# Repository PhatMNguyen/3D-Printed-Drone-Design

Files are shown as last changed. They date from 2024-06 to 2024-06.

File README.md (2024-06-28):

UTA has held the 3D-Printed Aircraft Competition (PAC) for eight years. A rotatory 
drone was 3D printed through additive manufacturing to compete in the 3D-printed aircraft 
competition. The drone was developed in several parts, including electronics, drone frame, arms, 
and drag device. Each component was designed and researched to be lightweight with minimal 
vibration and stiff structure. The electronics were chosen to ensure enough thrusting force and 
power to withstand the weight of the drone and drag device. The 3D filament chosen for the 
drone is abs, which was chosen based on its performance to heat, low density, and high elastic 
modulus, ensuring a stiff structure. Using topology optimization and solid works a 5” arm was 
created with stiffness and weight as our main objective. The drag device was created as a hinge, 
so the flaps were able to descend slowly, our main goal was to increase surface area without any 
electronic actuation. The design was further improved and tested through simulation and 
experimentation to ensure maximum stiffness, minimum frequencies, fast response and stable 
flight. The progression from the start to the final design took many iterations, but each iteration 
improved the overall design. The final iteration of our design was able to achieve 30 feet in the 8 
second time frame and a free fall time of 3 seconds.

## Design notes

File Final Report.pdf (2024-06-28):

# 3D Printed Drone Drone C Spring 2024

# Final Report

By
DESCENDER Inc.

Hoa Nguyen
Peter Nguyen
Yugesh Shrestha
Phat Nguyen
Cavin Van

Prepared for
Dr. Woods
Dr. Allsup
Dr. Taylor

May 3, 2024

Page | i

Abstract
UTA has held the 3D-Printed Aircraft Competition (PAC) for eight years. A rotatory drone was 3D printed through additive manufacturing to compete in the 3D-printed aircraft competition. The drone was developed in several parts, including electronics, drone frame, arms, and drag device. Each component was designed and researched to be lightweight with minimal vibration and stiff structure. The electronics were chosen to ensure enough thrusting force and power to withstand the weight of the drone and drag device. The 3D filament chosen for the drone is abs, which was chosen based on its performance to heat, low density, and high elastic modulus, ensuring a stiff structure. Using topology optimization and solid works a 5” arm was created with stiffness and weight as our main objective. The drag device was created as a hinge, so the flaps were able to descend slowly, our main goal was to increase surface area without any electronic actuation. The design was further improved and tested through simulation and experimentation to ensure maximum stiffness, minimum frequencies, fast response and stable flight. The progression from the start to the final design took many iterations, but each iteration improved the overall design. The final iteration of our design was able to achieve 30 feet in the 8 second time frame and a free fall time of 3 seconds.

Page | ii

Personnel

Hoa Nguyen
Lead Engineer
hoa.nguyen6@mavs.uta.edu

Peter Nguyen
Analysis Engineer
petertung.nguyen@mavs.uta.edu

Phat Nguyen
System Engineer
phat.nguyen4@mavs.uta.edu

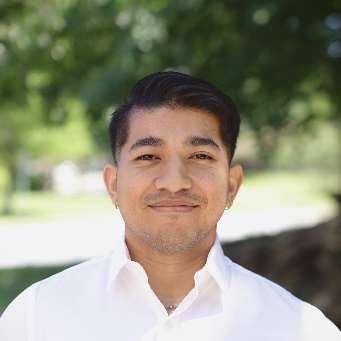
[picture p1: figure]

Yugesh Shrestha
Design Engineer
yugesh.shrestha@mavs.uta.edu

Cavin Van –
Manufacturing Engineer–
cavin.van@mavs.uta.edu

Faculty Advisors
Dr. Taylor
taylorrm@uta.edu

Dr. Allsup
thomas.allsup@uta.edu

Page | iii

Table of Contents

Page | iv

Nomenclature
a - Acceleration [m/s² ]
A - Surface Area [m²
| ]
C - Coefficient [-]
D - Drag Force [N]
F - Force [N]
g - Gravity [m/s² ]
H - Height [m]
L - Length of Arm [mm]
m - Mass [kg]
M - Moment [N*mm]
ρ - Density [kg/m³ ]
P - Power [W]
R - Reaction Force [N]
t - Time [s]
T - Torque [N*mm]
v - Velocity [m/s]
V - Shear [N]
ω | - Angular Velocity [rad/s]
x | - Location [mm]

Subscript
d | - Drag
f | - Final
i | - Initial
t | - Terminal
total - Total

Page | 1

### 1. Introduction

With the recent technological advancement of additive manufacturing, it has been widely popular in today’s manufacturing process. One form of additive manufacturing is called fused deposition modeling (FDM) 3D printing. With the advancement of FDM 3D Printing, it is widely used for rapid prototyping due to its consistency, reliability, and fast printing. Not only can FDM 3D printing be used for rapid prototyping, but it can also be another manufacturing method to produce parts for a product. With that, this project aims to use FDM 3D printing for rapid prototyping and producing a drone model that is completely 3D printed and functional.

### 2. Motivation

This is the 8th annual 3D-Printed Aircraft Competition (PAC) that UTA has hosted. Where students will compete to develop a 3D-printed aircraft using additive manufacturing. Currently, there are two aircraft categories: fixed and rotary wing. For the rotary wing category, students will create an aircraft where lift is generated by the propelling motion of the motors. Students will also compete in design and overall flight time when only 8 seconds of power is given to fly 30 feet. This means the team with the longest overall flight time, ascending and descending the aircraft, will win the competition.

Figure 1 Competition Poster

## 3DPAC 2024

8

th Annual
3D Printed Aircraft Competition
University of Texas at Arlington
Registration Open Now

Registration Deadline: January 31, 2024
Design Report Submission deadline: May 31, 2024 Aircraft check-in date: July 12, 1:00 to 4:00 p.m.
Flyoff Date: Saturday, July 13, 2024

Location: University of Texas at Arlington Maverick Stadium

Fixed Wing Category
All lifting surfaces must remain fixed • Altair Most Innovative Design*, $1000 • Longest duration flight, first prize, $1000 • Longest duration flight, second prize, $500 Each team must complete an entry form by the registration deadline. Rules and online entry: http://uta.engineering/3DPAC and https://www.asc-composites.org/competitions For informative videos on how to accomplish lightweighting, optimization, and analysis in Altair Inspire, go to https://www.youtube.com/watch?v=knB5rH1usr4. For Questions or Sponsorship Inquiries: Robert Taylor (taylorrm@uta.edu) *Design reports must be received by submission deadline to be eligible for Altair Most Innovative Design Awards

Rotary Wing Category
A significant proportion of lift is generated by rotation of components or of the entire body • Altair Most Innovative Design*, $1000 • Longest duration flight, first prize, $1000 • Longest duration flight, second prize, $500

Page | 2

The goal is to create the final drone product to compete in the rotary aircraft category and fly off on July 13, 2024. The project aims to win the longest flight duration using the 3D-printed drag device and drone.

### 3. Theory

### 3.1. Drone Arm

The drone arm can be seen as a cantilever beam supported by the frame. When a propeller is added to a motor, the lift load is applied to the arms' ends. Figure [x] displays the arm's free-body diagram.

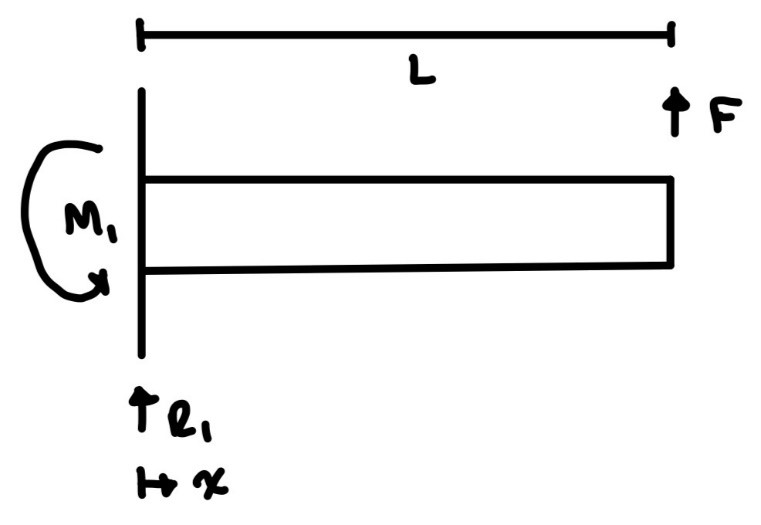
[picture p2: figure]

Figure 2 Free-Body Diagram of Drone Arm

To calculate the reaction forces, use the principle of equilibrium and have the sum of forces equal zero. The resultant forces can be found below.

R = F

M = F ∗ L

With the help of singularity equations, shear and moment can be found in the equation below.

V = M < x >+ R − F < x − L >

M = −M + Rx − F < x − L >

Page | 3

With the full analysis of this equation, the max shear will occur throughout the whole arm. The max moment will occur at the resultant forces; this is useful to determine the length of the arm to minimize this moment.

### 3.2. Drag Device

The design of the drag device was based on increasing the surface area to increase the drag force experienced by the device, which would lead to an increase in descent time. Descent time was calculated first by determining the terminal velocity that the device was traveling before hitting the ground. The formula used to calculate the terminal velocity of the device is shown below.
v =
2W
CρA

Where Vt is the terminal velocity of the device once it enters free fall, ρ is the density of the air, A is the surface area of the drag device, and W is the weight, C is the drag coefficient of the drag device.

Initially, the flat plate's drag coefficient was used to calculate the terminal velocity. Weight was calculated by determining the material's volume and density. The gravity and density of the air at 90 degrees Fahrenheit at a Latitude of 32.73, a longitude of -97.11, and an elevation of 189.89 above sea level were used.

Time of descent was calculated in two phases; 1st phase was when it took the device to get to terminal velocity from the free fall, and 2nd phase was when it took the device to hit the ground after reaching terminal velocity. The formula used for this calculation is as follows:

1

st phase:

t =

v − v
g

where the initial velocity is zero, the final velocity is the terminal velocity, and g is the acceleration due to gravity. The distance traveled to reach terminal velocity was also calculated using the following formula shown below:

H =

v

− v

2g

2

nd phase:
Given that the drone is estimated to drop from a height of 9.14m (30ft), the time it took to reach the ground after reaching terminal velocity was calculated using the following formula.

Page | 4

t =

9.14 − H
v

The total time of descent was calculated by adding those two times together.

t = t + t

### 4. Design

### 4.1. Drone Specification

Protecting the electronic components in the drone body was ideal. A modular design, where the arms can be replaced, would have been ideal if the arms had been destroyed in the flight tests. A lower center of gravity is crucial to the design as it helps the overall stability of the device. A stiff structure reduces vibrations in the system, or instability can occur.

### 4.2. Drag Device Specification

The drag device was designed by keeping the weight of the device and the drone’s main body in mind. The goal was to stay under 600 g for the entire assembly. Weight reduction was also achieved by having the drag device deploy with the help of air resistance instead of servos.

### 4.3. Electronic Specification

- Flysky remote control and receiver.
This allows the remote controller to communicate with the drone and receive any controls.
- 4 Cells LiPo battery; 650mAh, 90C, 15.8V
A 650mAh (0.65Ah) battery with a 90C discharge rate can provide 90 times its capacity. So, 90 x 0.65Ah = 58.5A, which means the battery can safely provide 58.5A amps of current for 30 seconds.
- Xing 2208 1800kv motors
2208 => stator’s diameter = 22mm and height = 8mm, 1800kv=> 1800 rpm per volt of the power supply. KV rating indicates the motor’s RPM per volt. At 22.2V, the motor’s theoretical maximum RPM is 1800 * 14.8 = 26640 RPM.
- Nazgul F5 – Tri Blade Propeller – 5.0x3.5x3
5-inch diameter = 0.127, 3.5-inch pitch
- SpeedyBee F405 V4 BLS 55A 30x30 FC&ESC Stack

Verification:

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

Page | 6

=> total discℎarge rate = 12

=> Battery time ∶ 225s

So, with the chosen components, the motor can produce sufficient power to achieve the goal with a discharge rate of 12. The thrust calculation was computed with a blade efficiency of 80%. Blade-Element Theory (BET) and Vortex theory must be considered for more accurate thrust predictions. The theoretical battery time is calculated to be 225 seconds, equivalent to 3.75 minutes, sufficient for three flights in competition.

Torque (τ) calculation:

Power (P) =

τ
ω

=> τ = Pω = 16W ∗ 4185.5

rad
s

= 66968 N ∗ m = 66.96N ∗ mm

### 4.4. Material Selection

The materials investigated for this project were TPU, PLA, PETG, and ABS. The main criteria for choosing a material were based on a high heat resistance material, high elastic modulus, and low density.

Table 1 Material Properties

Materials | Heat Resistance Temperature (C) | Elastic Modulus (MPa) | Density (g/cm³ )
TPU | N/A | N/A | 1.22
ABS | 87 | 1880 | 1.05
PLA | 57 | 2750 | 1.24
PTEG | 69 | 1670 | 1.25

A highly heat-resistant material would be more resistant to softening as temperature increases. Materials with low heat resistance would likely soften and deform in the summer. For instance, PLA is affected by UV light weathering, which reduces the material's softening temperature, so using PLA for the final device is not advised. However, because PLA is very easy to use when 3D printing, it is ideal for prototyping compared to the other materials.

Investigating the material's elastic modulus can achieve high stiffness, resulting in the arms having a very small deflection when loads are applied. The best materials would be ABS and PLA because they would allow for higher stiffness in the arms, whereas TPU is very elastic and works best as a damper.

Page | 7

A material with the lowest density would allow the drone to be lightweight, increasing the time of our descent. ABS was chosen because it has the highest heat resistance temperature, the lowest density, and the second-highest elastic modulus.

### 4.5. Arm Design 1

The first design is displayed in Figure 3. This model ultimately did not work, as the arms were too long and caused the structure to break at the root of the arms. With that, it was too heavy and was weak when it came to torsional. A vibration test was run to determine if the system would experience any vibrations. The results from the vibration test showed that there were vibrations in the system, which would cause instability. So, a redesign of the arms will be considered to combat the vibration issues.

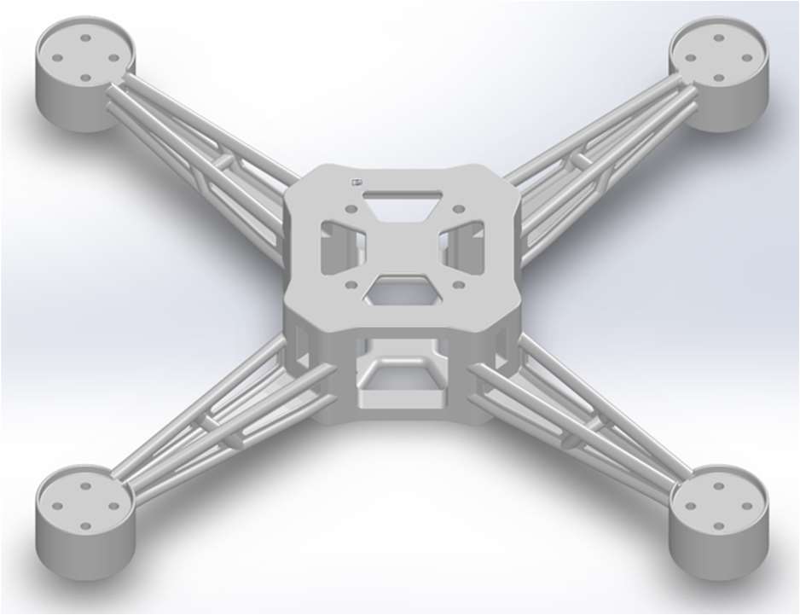
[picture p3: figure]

Figure 3 1st Iteration Arm

### 4.6. Arm Design 2

From the first design, where there were issues at the root, the drone arm length was shortened to reduce the moment at the root. The design goal of the arms is to keep them stiff and lightweight. With the help of topology optimization, the drone arm was designed and shown in Figure 4. The second iteration is designed to be stiff to combat the forces of lift and torsional at the end. Overall, this is a better design than the previous iteration due to its reduced moment at the root, stiffness, and lightweight. This structure will also help reduce vibrations experienced in the first iteration.

Page | 8

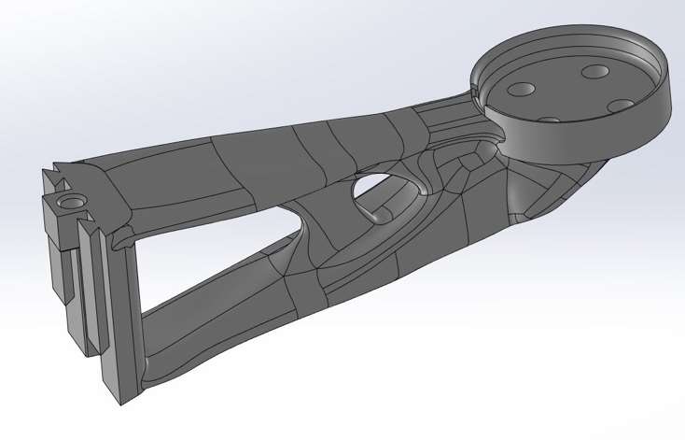
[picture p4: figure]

Figure 4 2nd Iteration Arm

### 4.7. Drag Device Design 1

The initial prototype of the drag device was created based on a modular design. The circular flaps at the end of the arms were to generate drag force. The arms could rotate vertically about the point of contact at the base. This design choice was made so that the drag device would deploy with the help of air resistance. During numerous tests of this prototype, it was observed that the circular flaps did not generate enough drag for the drag device to slow down. Still, the arm's ability to rotate vertically during deployment made the descent stable possible.

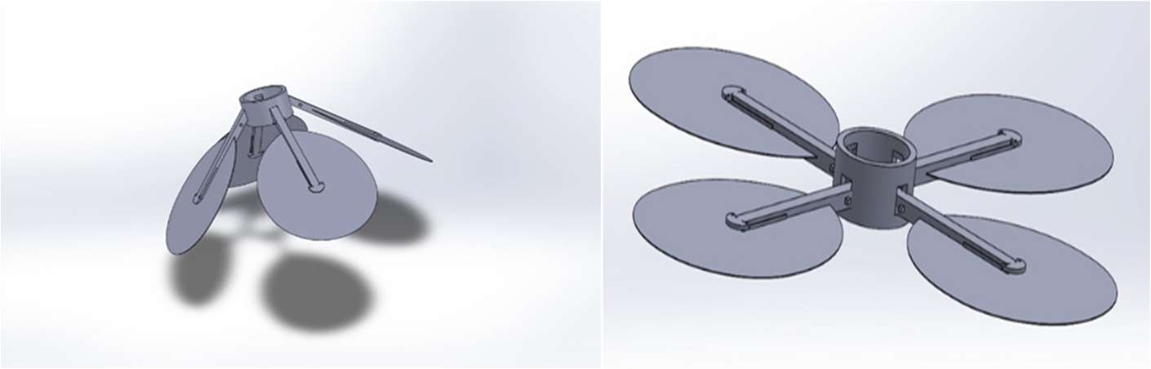
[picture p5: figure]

Figure 5 1st Concept of Drag Device

### 4.8. Drag Device Design 2

The second prototype was designed to direct the airflow underneath the drag device. The motivation for designing this prototype was taken from the sugar glider’s gliding motion during free fall. The curved wing design was incorporated to direct the airflow outwards from the center cross-section to achieve drag. While testing this prototype, the amount of surface area of the device helped generate enough drag force to slow down the device, but it was observed that the device had unstable descent on multiple test runs. The inability of the air to pass through the center created turbulence, which was the main reason for the unstable descent. Fixed wings also meant the rotors could not direct air to the ground to generate enough lift for the drone to fly.

Page | 9

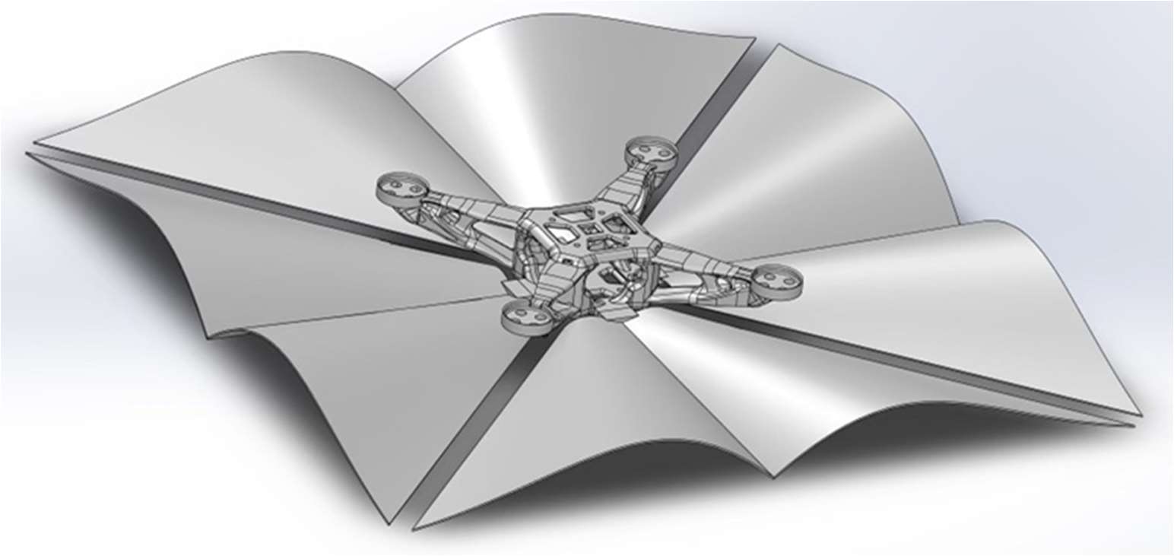
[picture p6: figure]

Figure 6 2nd Concept of Drag Device

### 4.9. Drag Device Final Design

The final design of the drag device was a collaboration of two previously designed prototype ideas. The flaps from the 2nd prototype were incorporated to deploy only due to air resistance. The hinge-like design between the flaps and the drag arm helped the flaps to rotate about the point of contact. Constraints for how much rotation the flaps can make were created by introducing stoppers on the arms, which also dictated the flaps' deflection. Positioning radially outward flaps helped create space at the center of the device, which would be crucial in directing airflow through the center. Pillar structures were assimilated between the drone and drag arms to support and stabilize the structure.

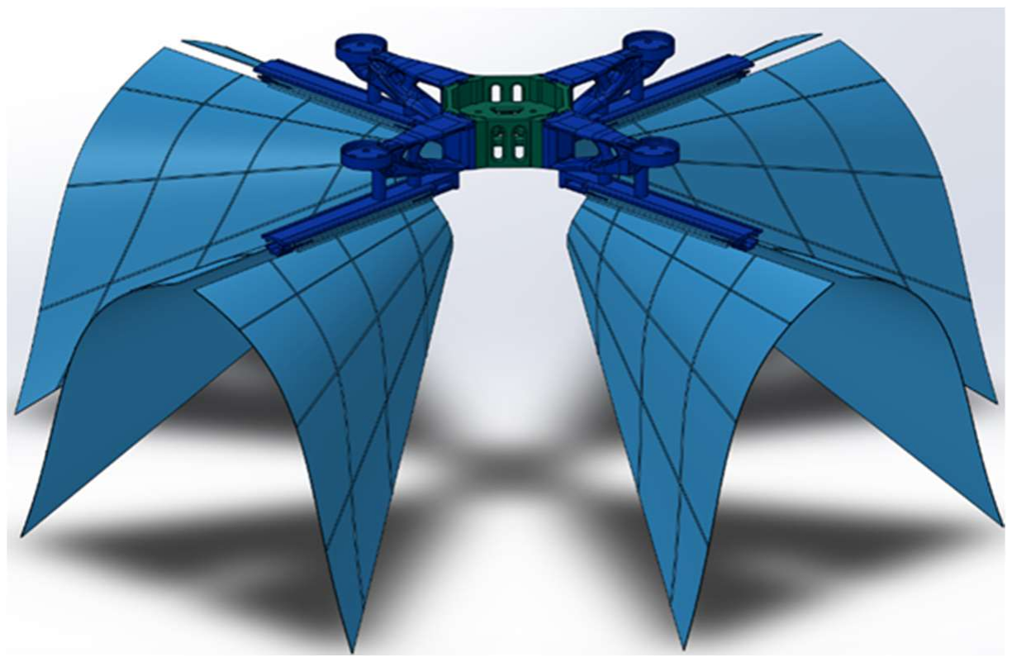
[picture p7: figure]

Figure 7 Current Design

Page | 10

### 5. Analysis

### 5.1. Drone Arm 2

The quadcopter drone's structural integrity and performance were evaluated using finite element analysis on ANSYS. For structural analysis, the purpose was to examine the drone's behavior under different loading conditions, including its weight and aerodynamic forces, such as the thrust force. The drone's weight acts as a downward force at the center mass of the drone. The thrust force from each propeller generates lift and acts as an upward force. Each arm was modeled as a cantilever beam, fixed at one end and free at the other. There were fixed supports placed at the screw holes of each arm, where it was connected to the base of the drone. The lifting force and weight were also accounted for.
The structural analysis results calculated the total deformation, Von Mises stresses, and safety factor. The results of total deformation showed a uniform deformation, where a maximum total deformation of 0.063 mm occurred at the propellers and decreased uniformly towards the screw holes to a minimum total deformation of 0 mm. It signifies that the drone had a high stiffness. A safety factor of 15 indicates that the drone was overdesigned, with unexpected loads. Although these were the results for the safety factor in ANSYS, the safety factor for the actual drone decreased due to the infill percentage, assuming solid infill when 3D printing the drone.

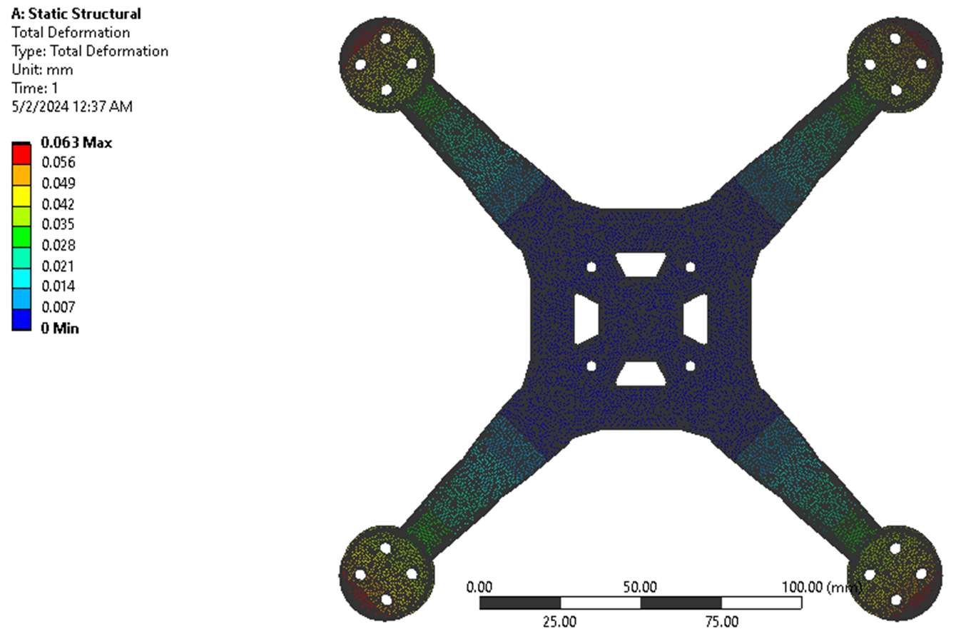
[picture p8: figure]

Figure 8 Total Deformation for Static Structural

Using Modal analysis in ANSYS, the drone's dynamic structure was identified by the mode shapes and their natural frequencies at different dynamic loadings or sinusoidal inputs of varying frequencies. This is where the structure experienced high-level vibrations and critical areas to add stiffeners to the part.

Page | 11

The analysis's results showed that the critical areas were at the ends of the arms, where it acted like a fixed free cantilever beam with loading applied at the free end. It showed that it is more likely to deflect at the tip at different dynamic loadings. The results showed that at the lowest frequency of 451 Hz, it would most likely resonate and vibrate, ultimately leading to stability and part failure when flying the aircraft. For the drone with the propellers and motors, it never reached 451 Hz, so the drone did not cause vibrations.

Figure 9 Total Deformation for Modal

### 5.2. Drag Device

Computational fluid dynamics simulation was conducted in SolidWorks using flow simulation. During the simulation, a metric unit system was chosen, and an external analysis was conducted with gravity turned on in the negative Y direction. The fluid for the simulation was air, and the terminal velocity of the device and its direction were entered. The type of flow was assumed to be laminar for this experiment. An Automatic Computational domain was created to conduct the Drag experiment. The global goal was created to track normal force in the Y direction, and the equation was entered to obtain the drag coefficient. The equation used to calculate the drag coefficient is shown below:

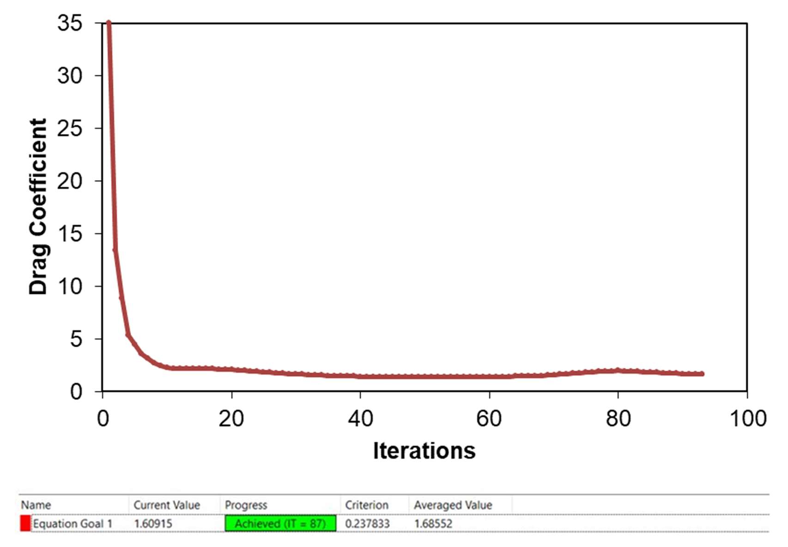
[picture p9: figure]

Page | 12

C =

2D
V

ρA

Where, C is the drag coefficient, D is the drag force, Vt is terminal velocity, ρ is the density of the air, and A is the device's surface area.
Quality Mesh is created to obtain adequate results for the calculations. Refinements were placed in a region surrounding the flaps because they are essential to the device's function.
Once the simulation started, plots were created, and the program continued running the simulation until the goal values, i.e., the Drag coefficient in this case, converged. A graph of converging values is shown in the figure below:

Figure 10 CFD Analysis Results

From 87 iterations, the average value of the drag coefficient was 1.69.

Cutting plots on the results helped to select the plane and parameter we wanted to inspect, which were shown in color contours depending on the values. Velocity distribution around the drag device is shown in the figure below:

Page | 13

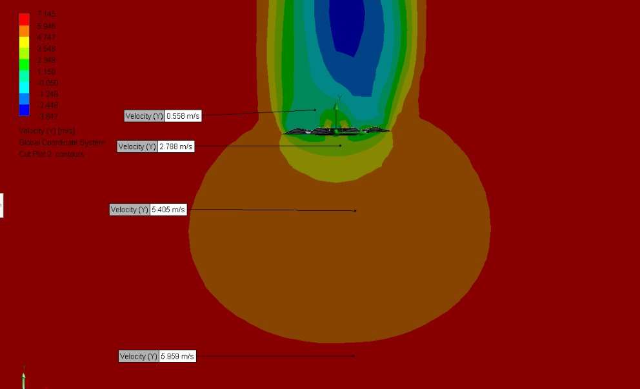
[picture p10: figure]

Figure 11 CFD Analysis

The drag coefficient obtained from the flow simulation was used to calculate the drag device's descent time. The table below shows the descent time of the drag device with an
increase in surface area.

Table 2 Time of Descend Calculation Based on Surface Area

Length (m) | Area (m² ) | Vt (m/s) | Drag force (N) | Time to reach Vt (s) | Distance to reach Vt (m) | Time to landing (s) | Distance to landing (m) | Total time for descent (s)
0.3 | 0.09 | 6.58 | 3.79 | 0.67 | 2.21 | 1.05 | 6.93 | 1.73
0.4 | 0.16 | 5.21 | 4.22 | 0.53 | 1.39 | 1.49 | 7.76 | 2.02
0.5 | 0.25 | 4.44 | 4.77 | 0.45 | 1.00 | 1.84 | 8.14 | 2.29
0.6 | 0.36 | 3.95 | 5.45 | 0.40 | 0.80 | 2.11 | 8.35 | 2.52
0.7 | 0.49 | 3.63 | 6.26 | 0.37 | 0.67 | 2.34 | 8.47 | 2.71
0.8 | 0.64 | 3.40 | 7.18 | 0.35 | 0.59 | 2.52 | 8.55 | 2.86
0.9 | 0.81 | 3.23 | 8.23 | 0.33 | 0.53 | 2.66 | 8.61 | 2.99
1 | 1 | 3.11 | 9.40 | 0.32 | 0.49 | 2.78 | 8.65 | 3.10

Page | 14

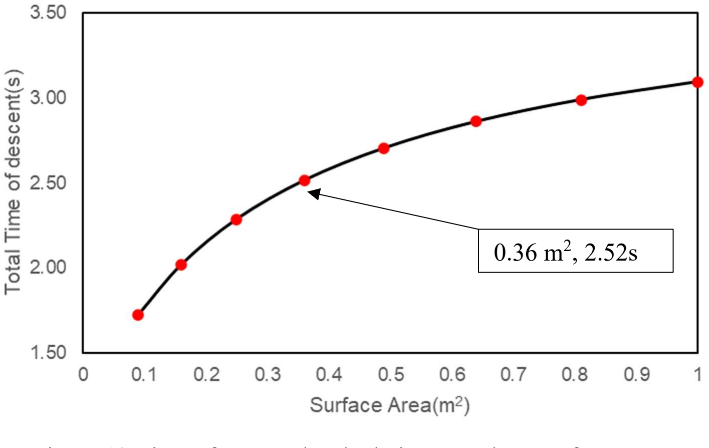
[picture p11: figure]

Figure 12 Time of Descend Calculation Based on Surface Area

### 6. Testing

### 6.1. Vibration Testing

During this test, the propellers will be removed from the drone, and the motors will be powered from 100 % and decreased to 40%. The structure will then be placed on a firm flat surface. During this test, it is important to observe any vibrations that the structure may encounter when the motors are at a constant 40% power. For the 1st iteration of the arms, it was found that there were vibrations present in the test. This led to the redesign of the arms, which led to the 2nd iteration. With the repetition of this test, the 2nd iteration arm did not encounter any vibrations.

### 6.2. Flight Testing

The drone could fly upward and downward without many stability issues during its launch. This means sufficient power is supplied to the motors, and the drone's weight is adequate for takeoff. It also has a faster response time and minimizes overshooting and system instability. There were also no implications with the drag device and drone when ascending upward because the drag device did not open until free fall.

Page | 15

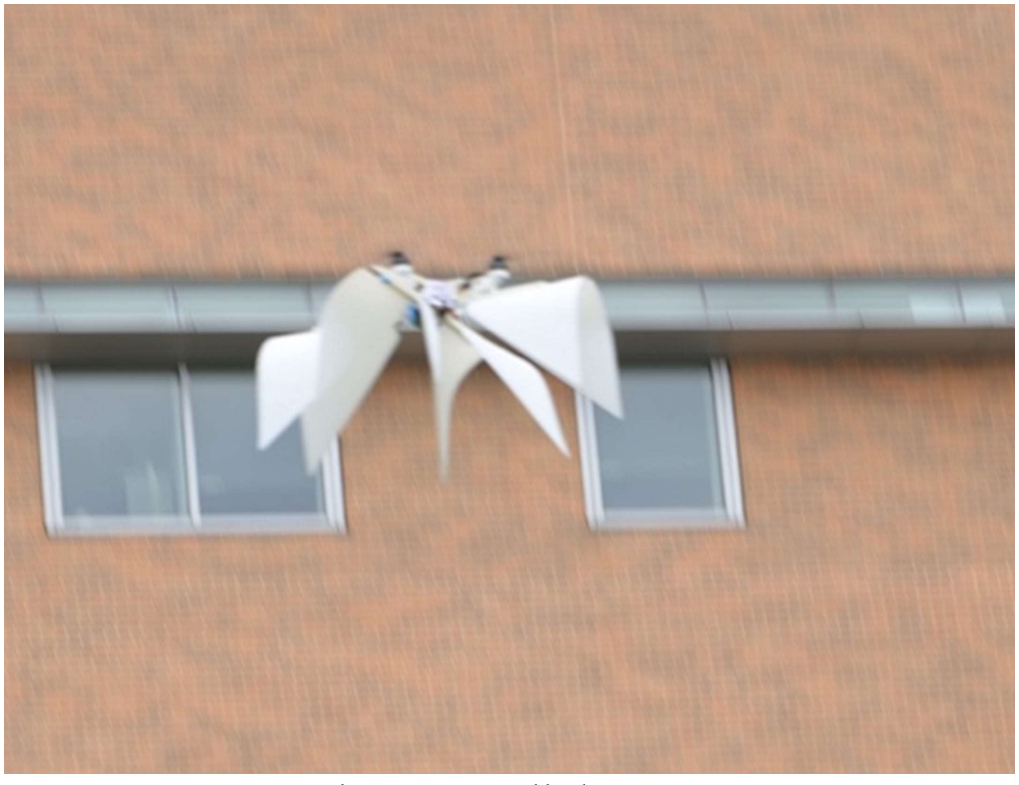
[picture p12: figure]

Figure 13 Flight Test

### 6.3. Drop Test

During the drone's descent and its drag device counterpart, the free fall time was 3 seconds. This fall time exceeded the calculated time of 2.52 seconds based on the 600 mm flaps. During the drag device's descent, the flaps worked just as anticipated, actuating like a hinge mechanism. During the drone’s descent, the flaps are met with air resistance, which opens the flaps, creating a drag force that slows the drone’s fall.

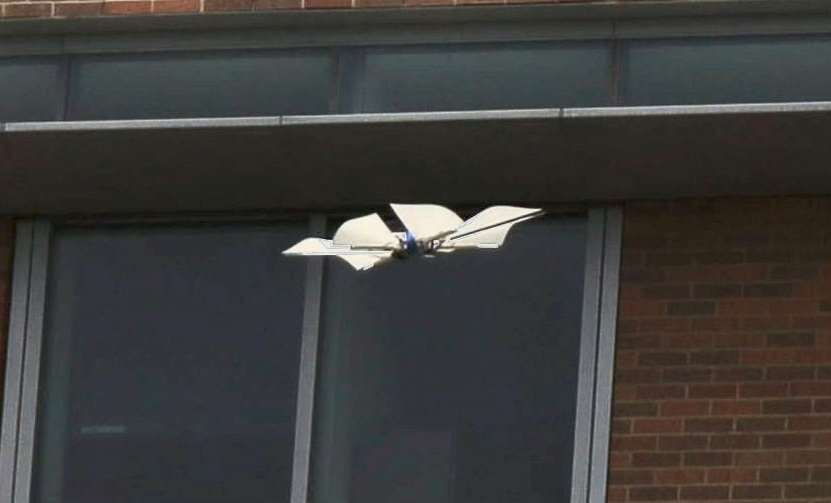
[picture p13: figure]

Figure 14 Drop Test

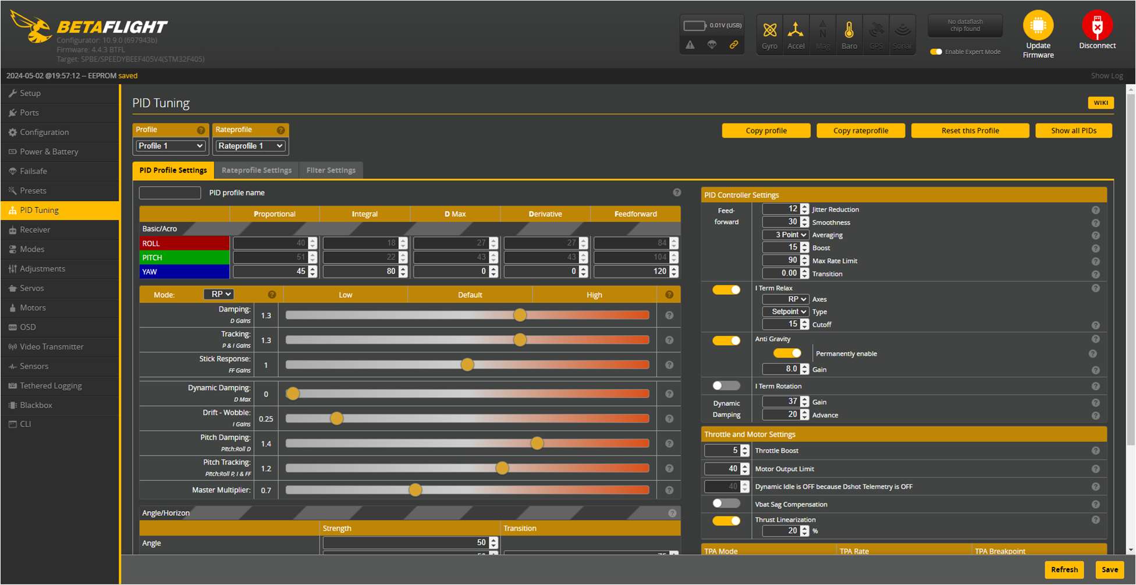
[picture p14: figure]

Page | 16

### 6.4. PID Tunning

Betaflight is utilized for Drone PID tuning, with adjustments made using the following sliders:

Figure 15 Betaflight Software

The tuning process begins by setting the initial tracking P&I slider value at 0.5, which is then incremented by 0.1 for each iteration. Flight tests are conducted for every increment to collect data into the drone’s Blackbox for dynamic response analysis in MATLAB. The responses are recorded for P &I slider values ranging from 0.5 to 1.3.

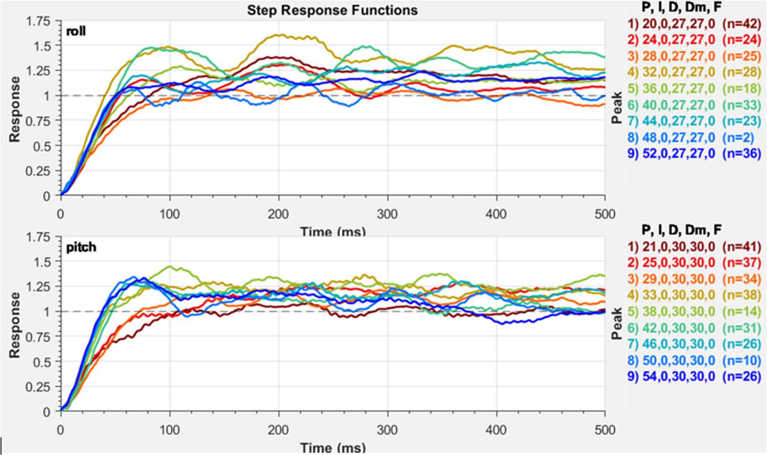
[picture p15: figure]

Page | 17

Figure 16 Dynamic Responses Corresponding to Slider Values

Among the responses, a value of 1.3 is chosen for its fast response and minimal oscillation for further tunning. However, a small steady-state error is observed in the roll response, and there is an overshot in the pitch response. To address these issues, the I-gain is increased for roll, and D-gain for pitch. The I-gain for Roll is adjusted by manipulating the "Drift-Wobble" slider, and the D-gain for Pitch is adjusted by manipulating the "Pitch damping" slider, using the same approach as adjusting the P&I slider.

Table 3 Sliders Values for Pitch Damping Test

Test Flight | Damping D Gain | Tracking P & I Gain | Stick Response | Dynamic Damping | Drift – Wobble | Pitch Damping | Pitch Tracking | Master Tracking
1 | 0.6 | 1 | 0 | 0 | 0 | 1 | 1 | 1
2 | 0.8 | 1 | 0 | 0 | 0 | 1 | 1 | 1
3 | 1.0 | 1 | 0 | 0 | 0 | 1 | 1 | 1
4 | 1.2 | 1 | 0 | 0 | 0 | 1 | 1 | 1
5 | 1.4 | 1 | 0 | 0 | 0 | 1 | 1 | 1
6 | 1.1 | 1 | 0 | 0 | 0 | 1 | 1 | 1

Page | 18

Table 4 Sliders Values for Multiplier Test

Test Flight | Damping D Gain | Tracking P & I Gain | Stick Response | Dynamic Damping | Drift – Wobble | Pitch Damping | Pitch Tracking | Master Tracking
1 | 1 | 1 | 0 | 0 | 0 | 1 | 1 | 0.60
2 | 1 | 1 | 0 | 0 | 0 | 1 | 1 | 0.75
3 | 1 | 1 | 0 | 0 | 0 | 1 | 1 | 0.90
4 | 1 | 1 | 0 | 0 | 0 | 1 | 1 | 1.05
5 | 1 | 1 | 0 | 0 | 0 | 1 | 1 | 1.20

Table 5 Sliders Values for I-gain Test

Test Flight | Damping D Gain | Tracking P & I Gain | Stick Response | Dynamic Damping | Drift – Wobble | Pitch Damping | Pitch Tracking | Master Tracking
1 | 1 | 1 | 0 | 0 | 0.25 | 1 | 1 | 0.9
2 | 1 | 1 | 0 | 0 | 0.5 | 1 | 1 | 0.9
3 | 1 | 1 | 0 | 0 | 0.75 | 1 | 1 | 0.9
4 | 1 | 1 | 0 | 0 | 1 | 1 | 1 | 0.9
5 | 1 | 1 | 0 | 0 | 1.25 | 1 | 1 | 0.9

Figure 17 Dynamic Responses Corresponding to I-Slider Values

Decreasing the master multiplier reduces noise in the signal, resulting in less vibration. The vibration in the signal can be recognized by the drilling sound emitted by the motor when the drone is hovering.

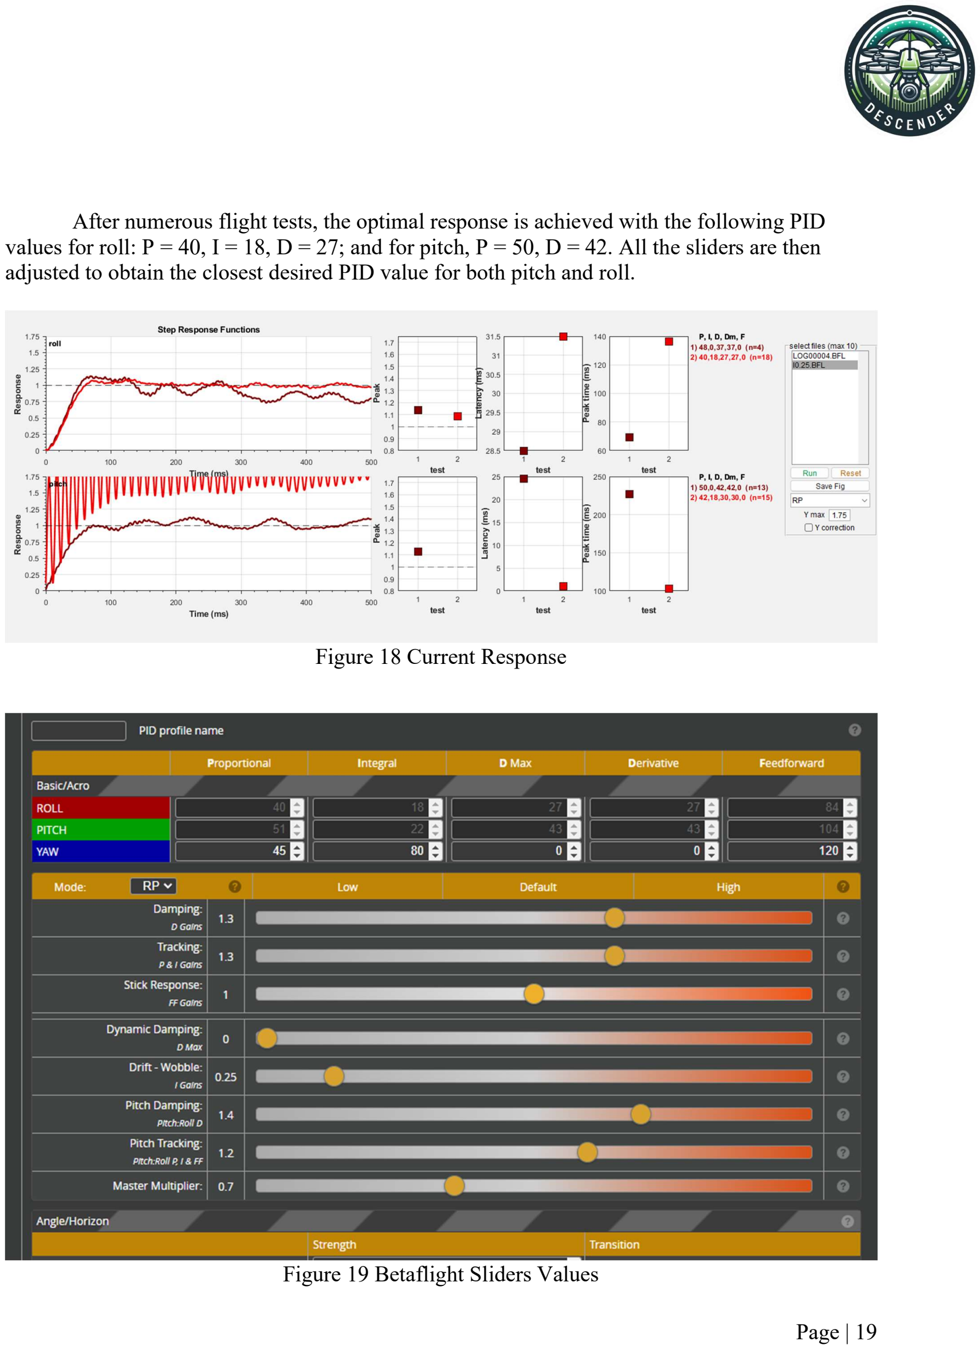
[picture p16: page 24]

Page | 19

After numerous flight tests, the optimal response is achieved with the following PID values for roll: P = 40, I = 18, D = 27; and for pitch, P = 50, D = 42. All the sliders are then adjusted to obtain the closest desired PID value for both pitch and roll.

Figure 18 Current Response

Figure 19 Betaflight Sliders Values

Page | 20

### 7. Results

### 7.1. Vehicle Performance

With multiple flight tests, the drone consistently performed the way it was intended to. The flaps hinged inwards when the drone ascended and hinged outwards when descending. A consistent test was a huge success and a great accomplishment in the semester.

### 8. Summary

A successful working prototype has been produced that can take flight. Proportional Integral Derivative (PID) tuning has been accomplished to ensure a faster and more accurate response to the control system for this current model.

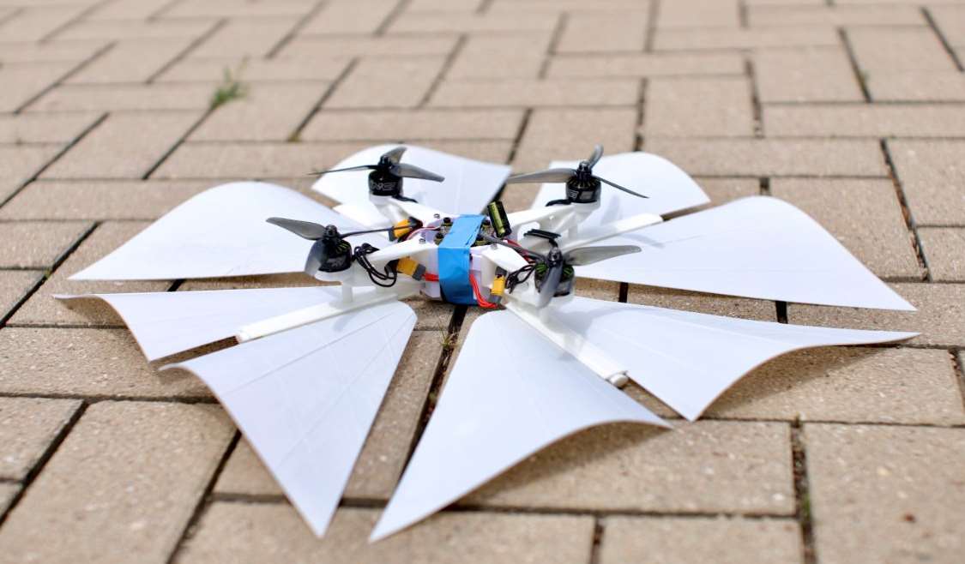
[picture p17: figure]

Figure 20 3D Printed Prototype

The 3D-printed drone achieved an experimental time of 3 seconds, which exceeded the calculated time of 2.52 seconds.

### 9. Conclusion

As the semester ended, some noticeable accomplishments included having a working prototype that, when dropped from 30ft, had a free fall time of 3 seconds. The steps to getting to having a working prototype took many iterations and design changes. Rather, there were issues with stability or vibrations. Each iteration made the structure more stable, prone to fewer vibrations, and a good learning experience. While a working prototype is a big accomplishment, there are numerous ways to improve the free fall time.

Page | 21

10.Future Work

Next semester's plan is to increase the drone’s descent time for the next semester. To accomplish this goal, two approaches can be investigated: increasing the surface area of the flaps and reducing the weight. While increasing the surface area of the flaps will dramatically impact the time of descent, it may lead to a challenge when it comes to printing.

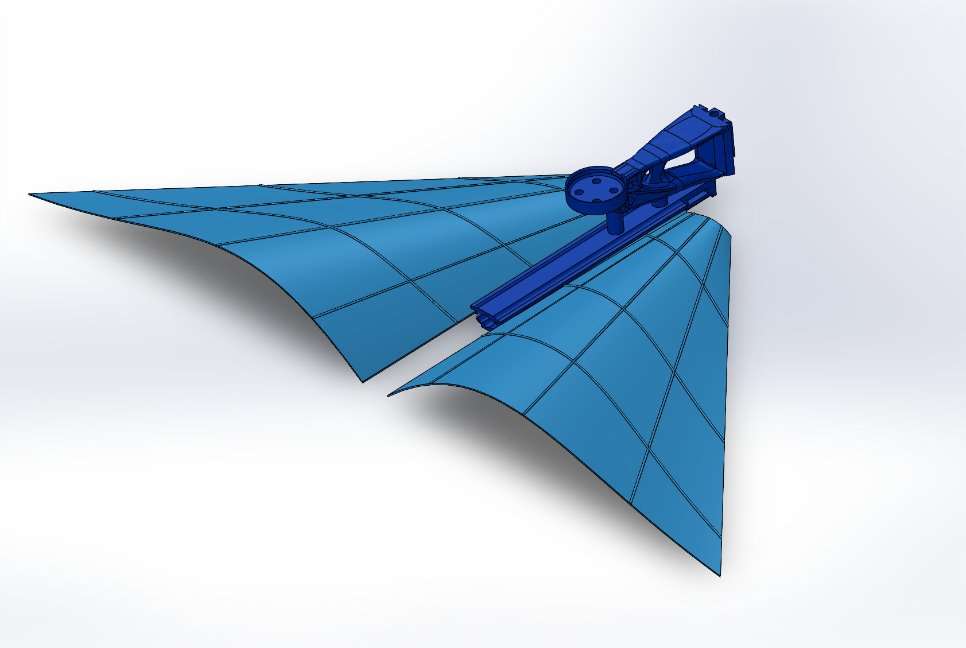
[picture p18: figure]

Figure 21 Current Design of the Flaps

Another note is that when the length of the flaps is increased, there is a constant breakage at the same spot. The future plans are to either increase the thickness of the flaps, create a thicker stiffener for the wings, or change the print orientation.

Page | 22

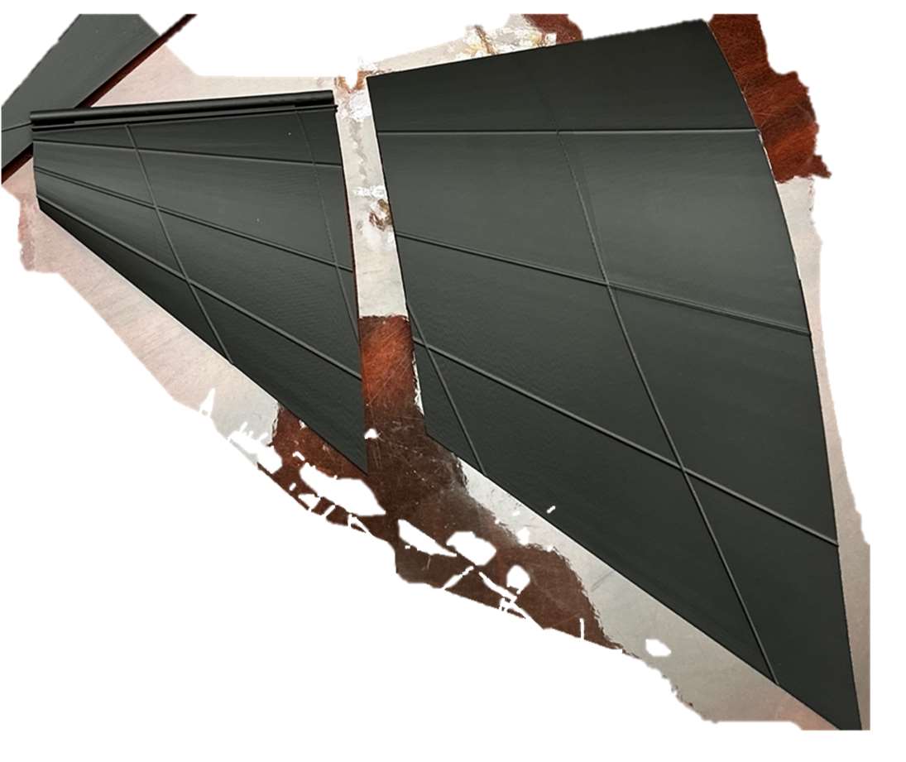
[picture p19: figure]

Figure 22 Breakage on Flaps

Reducing the weight of the overall drone will increase the time of descent. The infill density and pattern will be investigated without affecting the drone's performance. Also, the model should be looked at overall and investigated where any material can be removed without sacrificing structural integrity.

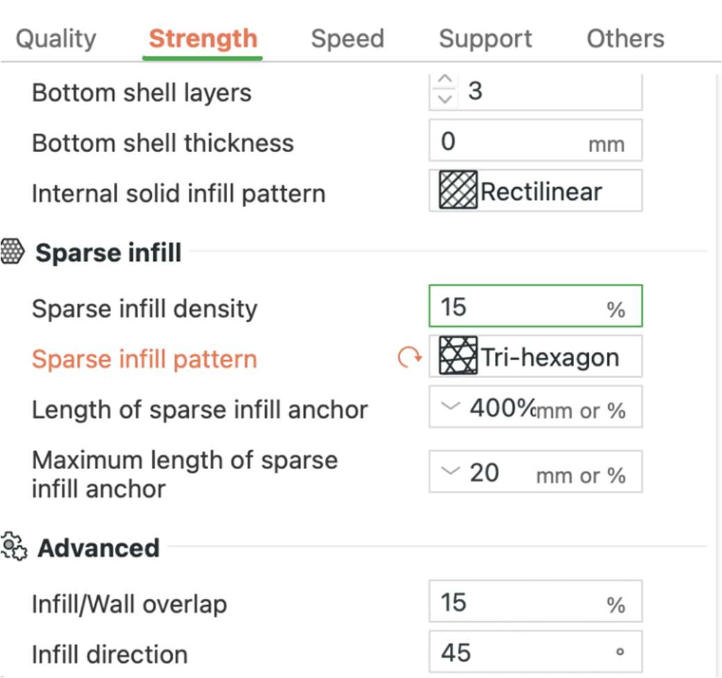
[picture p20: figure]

Figure 23 Changing Infill

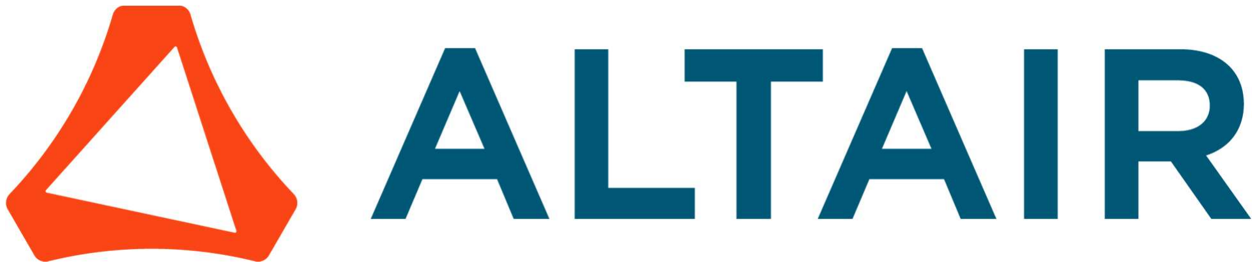
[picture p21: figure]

Page | 23

Acknowledgments

Event Coordinator
Dr. Taylor
taylorrm@uta.edu

Event Sponsors

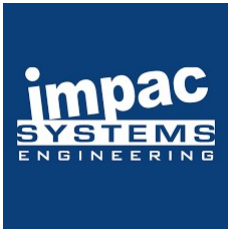
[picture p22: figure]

Page | 24

Page | 25

References

[1] 1Munson, B. R., Okiishi, T. H., Huebsch, W. W., and Rothmayer, A. P., Fundamentals of Fluid Mechanics, Hoboken, NJ: John Wiley et Sons, Inc., 2013.
[2] 1Goodno, B. J., and Gere, J. M., Mechanics of Materials, Boston, MA: Cengage Learning, 2018.

Appendix

### 1.1 Drone Arm 1 Analysis

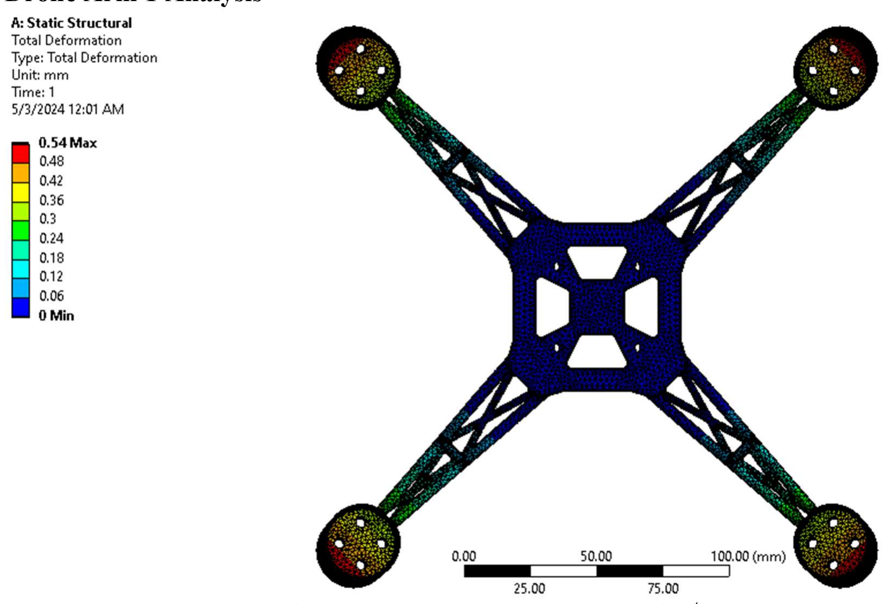
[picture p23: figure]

Figure 24 Total Deformation for Static Structural 1st Iteration Arm

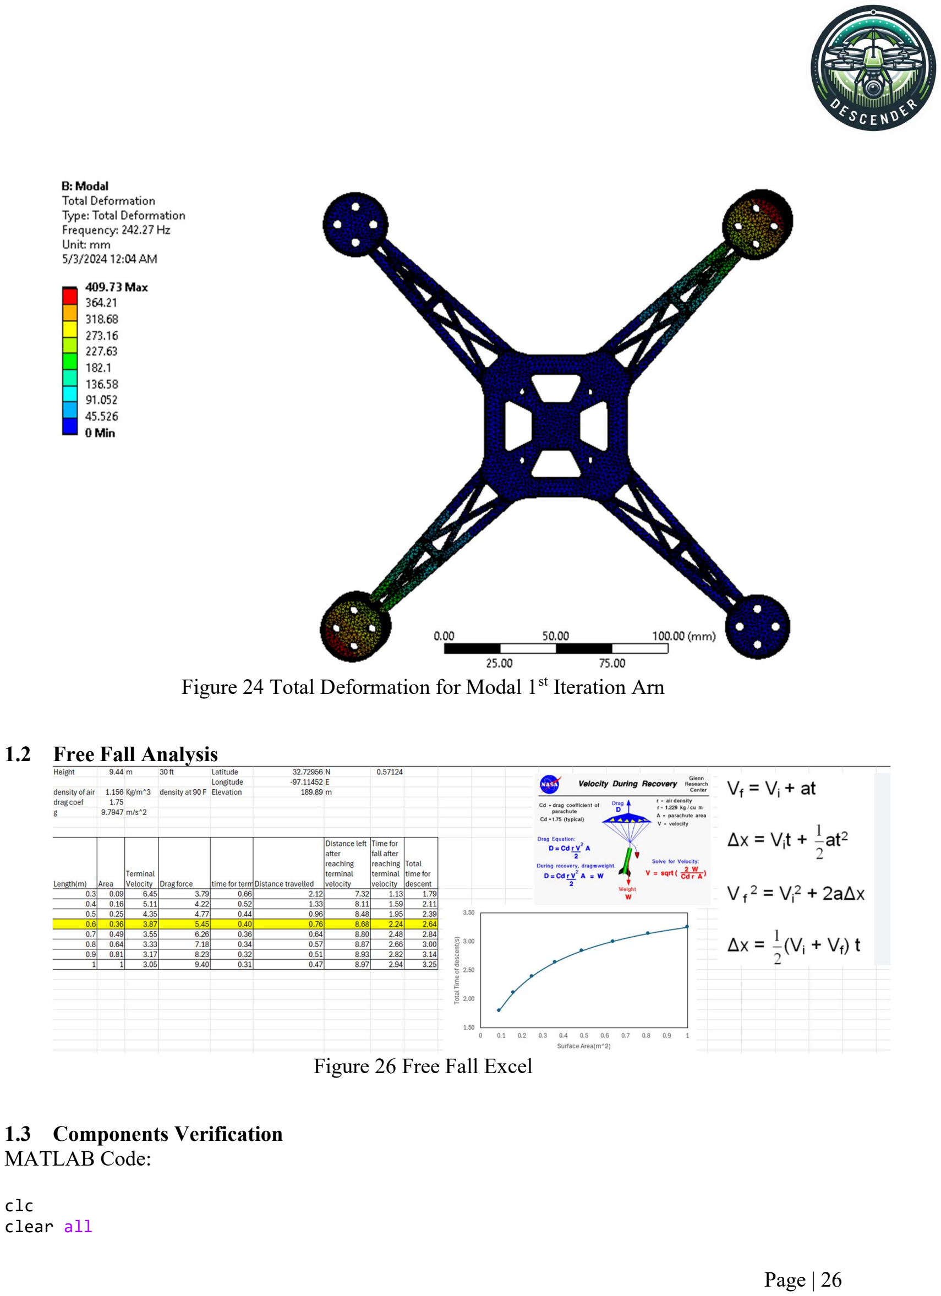
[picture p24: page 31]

Page | 26

Figure 24 Total Deformation for Modal 1st Iteration Arn

### 1.2 Free Fall Analysis

Figure 26 Free Fall Excel

### 1.3 Components Verification

MATLAB Code:

clc
clear all

Page | 27

format compact
format shortEng
% Given constants
mass = 0.68; % Mass in kg
g = 9.81; % Acceleration due to gravity in m/s^2 H_target = 9.144; % Target height in meters (30 ft) time = 5; % Time to reach target height in seconds V_battery = 22.2; % Battery voltage in Volts I_battery = 1.2; % Assumed current draw in Amps C=120; %discharge rate
I_battery_max = I_battery*C;
e_battery = 0.6; % Battery efficiency
e_Propeller = 0.8; % Propeller efficiency
rhoAir = 1.225; % Air density in kg/m^3
D_propeller = 0.155; % Diameter of propeller in meters (6.1 inches converted to meters)
% Calculating required acceleration to reach target height
a = (2*H_target) / time^2; % Acceleration in m/s^2
aTotal = a + g; % Total acceleration including gravity
% Calculating required force
F_required = mass * aTotal; % Force required in Newtons

% Calculating thrust per motor
T_motorReq = F_required / 4; % Assuming 4 motors
% Motor RPM calculation
KV_motor = 1800; % Motor KV rating
RPM = KV_motor * V_battery; % No-load RPM
% Power calculation
P_electrical = V_battery * I_battery_max; % Electrical power in Watts P_effective = P_electrical * e_battery;
T_motorProduce = (2 * rhoAir * pi * (D_propeller/2)^2 * P_effective^2)^(1/3) * e_Propeller; % Thrust in Newtons
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

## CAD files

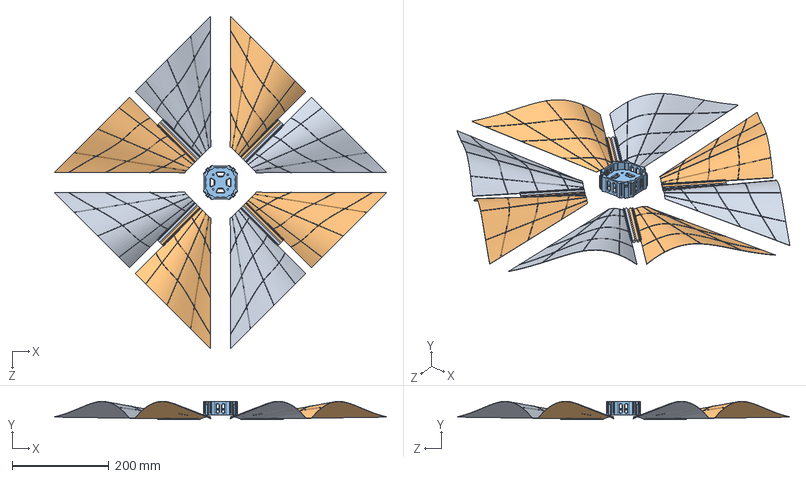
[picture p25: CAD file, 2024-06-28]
Solidworks_File_5_2_2024/DroneWDrag2.SLDASM
689.2 x 37.7 x 689.2 mm
Base_plate_3
Drag_Flap_Right x 4
Drag_Flap_Left x 4

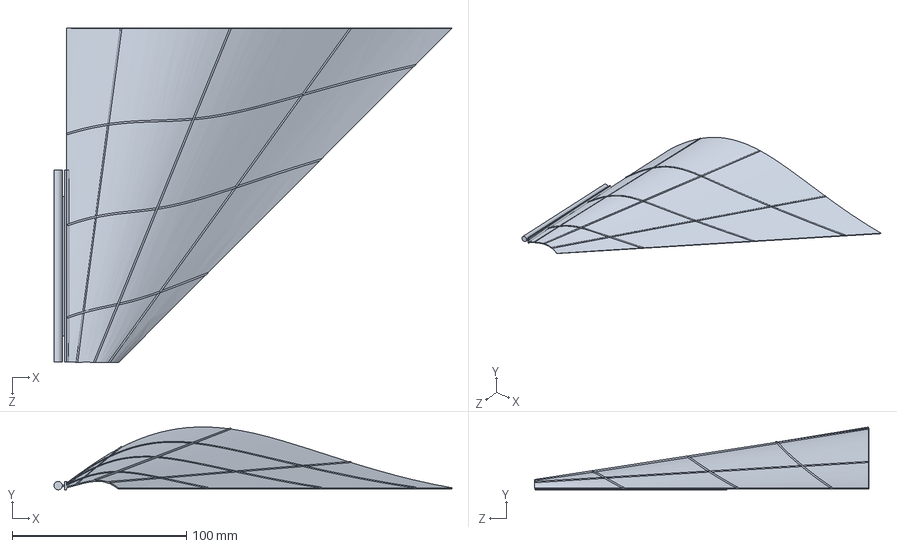
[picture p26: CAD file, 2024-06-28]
Solidworks_File_5_2_2024/Drag_Flap_Left.SLDPRT
228.1 x 36.1 x 191.7 mm

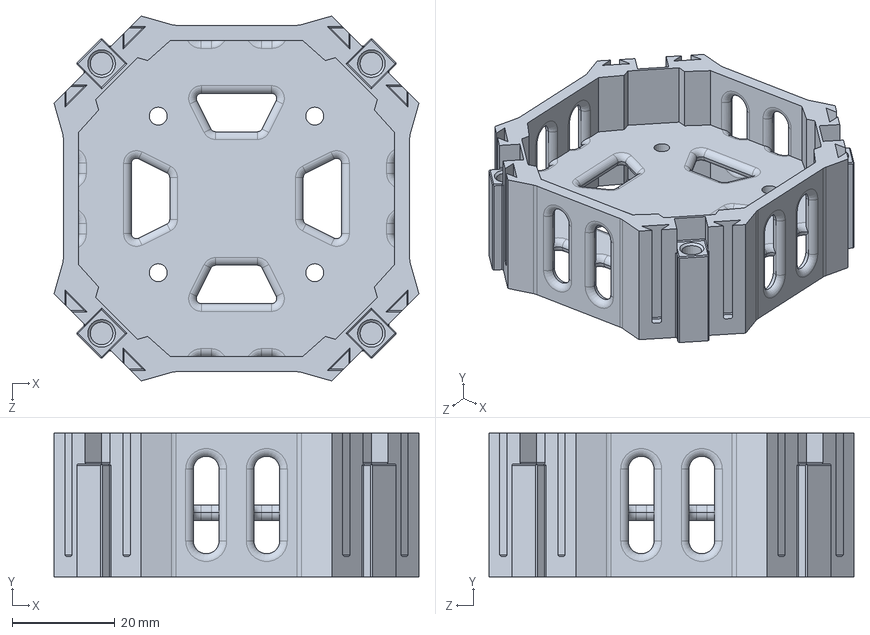
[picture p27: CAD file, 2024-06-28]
Solidworks_File_5_2_2024/Base_plate_3.SLDPRT
71.1 x 28.0 x 71.1 mm

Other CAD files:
Solidworks_File_5_2_2024/Drag_Flap_Right.SLDPRT
